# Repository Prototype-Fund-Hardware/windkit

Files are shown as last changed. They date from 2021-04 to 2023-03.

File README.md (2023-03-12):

<div align="center">
  

#### ⚠️ Caution: The windkit is still in development.Prototype not field tested yet!⚠️

#### ⚠️ Project is not recommended for reproduction!⚠️


  

</div>

___

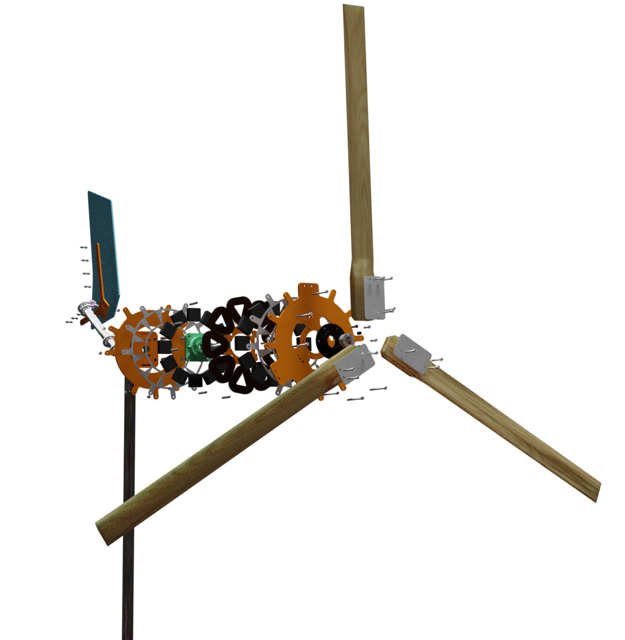
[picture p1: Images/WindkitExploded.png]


## Introduction

The windkit is a small wind turbine to generate electricity from wind energy. It can be used either in offgrid or ongrid applications. Apart from the [aluminium and steel parts](/-/tree/master/Export/LaserCutterFiles) that need to be laser cutted the windkit can be build and maintained using standard hand tools.

### Main features

- **secure**
- **easy to build, repair & maintain**
- **open-source**
- **developed following small wind turbine standard [IEC61400-2:2013](https://webstore.iec.ch/publication/5433)**

### Technical specifications

- **rotor diameter: 2.0 Meter**
- **rated power: 400 Watt @ 11 m/s wind speed**
- **energy production: 200 kWh/a @ 3 m/s annual average wind speed**
- **system voltage: 12, 24, 48 Volt**

For more information check out the [Flyer](./Misc/FlyerWindkit.pdf)!

### What the windkit can and can´t do:

#### What it can´t:

* It will not power your entire house and heat your swimming pool.

* It will not work on a balkony or a roof top.

* It will hardly deliver energy on a site with low or no wind. It's performance would then be like a photo voltaic module placed in a cellar.

#### What it can:

* Supply offgrid places with people who are aware of theire energy consumption. Best in addition with photo voltaic.

* Produce around 800 kWh of electrical energy in windy sights like costal areas or islands.

* Be a fun project of self empowerment.

## Who we are and where we come from

We are the [ERNI-Collective](https://www.erni-kollektiv.org/)  a group of around 10 people based in Germany with various professional backgrounds (renewable-, civil-, environmental-engineer, metalworker, woodworker). We are focusing on educational workshops in the field of renewable energies especially on small wind turbines (SWT). Since 2015, we are conducting educational workshops on how to build, install, operate and maintane SWT based on the plans of [Hugh Piggott](https://scoraigwind.co.uk/a-wind-turbine-recipe-book/). In 1978 Hugh Piggott started to develop a SWT to power his offgrid home in Scotland on Scoraig-Island. Since then he designed various SWT ranging from 1.8 m to 4.2 m rotor diameter and published various Recipe Books and Construction Manuals.

## Development of the windkit

In our educational workshops we mainly build the [2F SWT](https://scoraigwind.co.uk/2014/06/ebook-plans-for-2f-turbine-now-finally-published/) from Hugh Piggott. Its a turbine with 2 m rotor diameter and a generator build with ferrite magnets. Throughout the years we realised that it was difficult for people to follow the DIY-focused building instructions.The idea of a more modular SWT design using standard parts and modern manufacturing technologies (laser cutting) was born.
The result is the windkit. You can find all files of the windkit in this repo as well as a step by step assmebly guide in the [wiki](https://git.erni-kollektiv.org/erni/windkit/-/wikis/1.Introduction).
The generator design of the windkit is still based on the [2F Construction Manual](https://scoraigwind.co.uk/2014/06/ebook-plans-for-2f-turbine-now-finally-published/). The blade design is based on the master thesis of [Performance analysis and improvement of a small locally produced wind turbine for developing countries](file:///C:/Users/imman/Downloads/Nienke%20Hosman%20r.pdf) by N. Hosman.

## Software requirements

#### FreeCAD - view and edit CAD files

windkit is build with realthunder's FreeCAD fork : FreeCAD_assembly3 [2020.08.18](https://github.com/realthunder/FreeCAD_assembly3/releases/tag/0.11). To modify the model we recommend the same or even newer versions. For the assembly process we've been using the assembly workbench Assembly3. The workbench is bundled in the fork mentioned before, no addition installation are needed. In addition we use the Fasteners WB [V0.3.32 03 Sep 2020](https://github.com/shaise/FreeCAD_FastenersWB/tree/bbdcf82e55467523f5533179a896225213b0b5f1) for fasteners groups, this workbench needs to be installed separatly via the Addon-Manager in Freecad. 

#### QCAD - view dxf files

Export files of 2D shapes of the CAD modell for laser cutting have the format ".dxf". This is a common format. To view the .dxf-files download the the open source 2D CAD software [QCAD](https://qcad.org/en/).

#### MarkText - view and edit mark down files

All text files in the windkit repository as well as the windkit wiki are written in [Markdown](https://en.wikipedia.org/wiki/Markdown). To open and edit markdown files, like this README.md, download the mark down editor [MarkText](https://github.com/marktext/marktext).

## Assembly overview

The master assembly file is called `MainAssembly.windkit.FCStd`. All sub-assemblies are saved in different folders. The sub-assemblies are shown in the following image below. The [BOM](./Bom.ods) is also structured the way the Cad is organised.
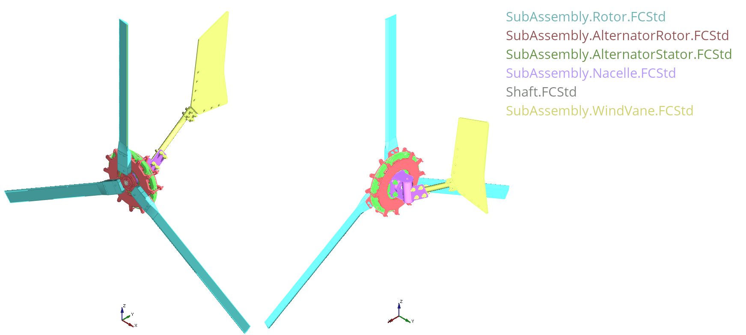
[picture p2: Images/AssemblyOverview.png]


## Prototype

Beginning of 2021 a prototype has been built in a workshop.
The following picture shows all parts of the windkit prototype before assembly. 

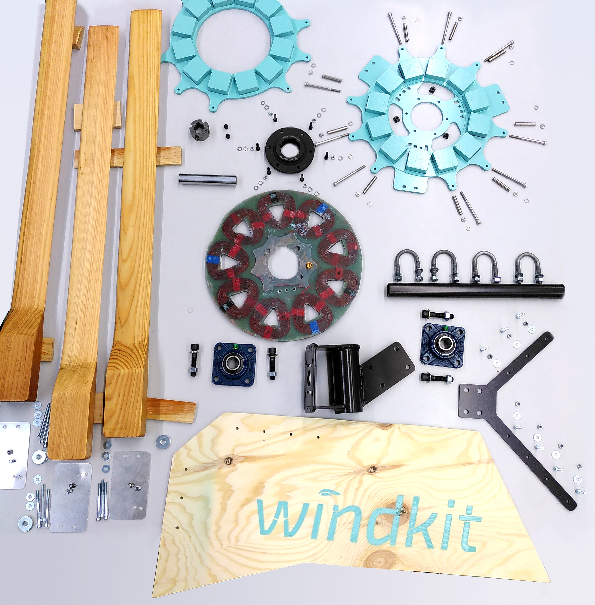
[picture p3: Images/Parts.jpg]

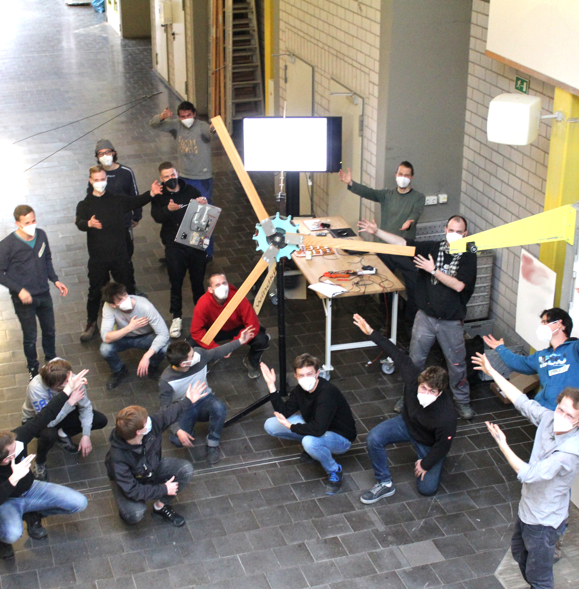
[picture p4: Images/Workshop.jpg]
  

The next step is to bring the turbine to the field for testing!

## Contributing

You want to contribute to our project? That´s great. Check out our [Contributing](https://git.erni-kollektiv.org/erni/windkit/-/wikis/Contributing)  page in our wiki.

## Get in touch with us

You wanna know more about this project or drink a beer with us? Just write us a message info@erni-kollektiv.org

windkit is developed by [ERNI collective](https://www.erni-kollektiv.org/)

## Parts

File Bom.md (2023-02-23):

The bill of materials (BOM) follows the BOM proposal of [DIN SPEC 3105](https://gitlab.com/OSEGermany/oh-tsdc/-/blob/master/OH-TsDC.md) using **TsDC-ID** (technology specific documentation criteria identifier) and unique position numbers to identify each component.

| TsDC-ID Abbreviation | Explanation |
| --- | --- |
| COM | Component |
| ASM | Assembly |
| BUY | Proprietary components |
| STD | Standard components |
| MAN | Self-designed components to manufacture |
| MEC | Mechanic |

| Pos. | Name | Units | TsDC-ID (1) | Reference |
| ---- | --- | ----- | --- | --- |
| 1 | rotor | 1 | ASM-MEC | |
| 1.01 | rotor front mounting plate | 3 | COM-MAN | Laser part, aluminium/stainless steel, 2 mm thick, RotorFrontMountingPlate.dxf |
| | | | | |
| 1.02 | rotor blade | 3 | COM-MAN | larch tree, air-dried, blade measurements: 1050 x 80 x 27 mm |
| | | | | |
| 1.03 | rotor blade fastener bolt | 9 | COM-STD | DIN 912 M6 x 50 mm, property class 8.8, metric bolt, cylinder head with hexagon socket |
| 1.04 | rotor blade fastener slot nut  | 3 | COM-STD | DIN 508-8-M6-8/10, T-Slot-Nut |
| 1.05 | rotor blade fastener nut | 6 | COM-STD | DIN 985 M6, hexagon lock nut, with polyamide clamping piece |
| 1.06 | rotor blade fastener washer | 6 | COM-STD | DIN 125 A M6, 6.4 x 12 x 1.6 mm, washer |
| 1.07 | boiled linseed oil | 1 | COM-BUY | 50 ml |
| 2 | alternator rotor | 1 | ASM-MEC | |
| 2.01 | upwind magnet disc | 1 | COM-MAN | Laser part, steel S235 or S355, 6 mm thick, no surface treatment, UpwindMagnetDiscSlotNut.dxf |
| 2.02 | taper bush | 1 | COM-BUY | Article ID.: 62250325,Taper bush 1210, bore 25 mm |
| 2.03 | taper bush setscrew | 2 | COM-STD | part of the scope of delivery of the taper bush, see pos. 2.02 |
| 2.04 | taper bush hub | 1 | COM-BUY | Article ID.: 14090120, Taper bush hub for Taper Bush size 1210, 120 mm outer diameter |
| 2.05 | taper bush hub fastener bolt | 6 | COM-STD | DIN 912 M6 x 25 mm, property class 8.8, cylinder head with hexagon socket |
| 2.06 | taper bush hub fastener nut | 6 | COM-STD | DIN 985 M6, hexagon lock nut, with polyamide clamping piece |
| 2.07 | taper bush hub fastener washer | 12 | COM-STD | DIN 125 A, for M6, 6.4 x 12 x 1.6 mm, washer |
| 2.08 | magnet stencil | 2 | COM-MAN | Laser part, aluminium/stainless steel, 2 mm thick, MagnetStencil.dxf |
| 2.09 | ferrite magnet | 24 | COM-BUY | Ferrit Magnet 50 x 50 x 20 mm |
| 2.10 | spacer sleeve | 9 | COM-BUY | Stainless steel sleeves 8 x 6 x 1 mm (up to M6), 50 mm length |
| 2.11 | discs fastener bolt | 9 | COM-STD | DIN 912 M6 x 85 mm, stainless Steel A2, metric bolt, cylinder head with hexagon socket |
| 2.12 | discs fastener nut | 9 | COM-STD | DIN 985 M6, stainless Steel A2, hexagon lock nut, with polyamide clamping piece |
| 2.13 | discs fastener washer | 18 | COM-STD | DIN 125 A, for M6, 6.4 x 12 x 1,6 mm, stainless steel A2, washer |
| 2.14 | downwind magnet disc | 1 | COM-MAN | Laser part, steel S235 or S355, 6 mm thick, no surface treatment, DownwindMagnetDisc.dxf |
| 2.15 | two component epoxy adhesive | 2 | COM-BUY | Two-component epoxy adhesive, min. 45 min hardening time |
| 2.16 | exterior metal paint | 1 | COM-BUY | 200 ml |
| 3 | shaft | 1 | COM-BUY | "Precision shaft steel CF53, hardened,  dressed to size, chromed, 25 (h7) x 1000mm: 64762500, per windkit 125 mm needed |
| 4 | alternator stator | | | |
| 4.01 | mounting inlay | 1 | COM-MAN | Laser part, steel S235 or S355, 6 mm thick, no surface treatment, MountingInlayUkf205Mt60.dxf |
| 4.02 | stator cast | 1 | COM-BUY | Epoxy resin and hardener, approx. 1.4 l |
| 4.03 | copper wire coils | 9 | COM-BUY | Approx. 3.6 kg of copper wire, 1.6 mm Diameter, Grade 2, 200°C heat resistant, approx. 400 g per coil, approx. 3.6 kg per windkit needed |
| 4.04 | mounting inlay fastener bolt | 4 | COM-STD | DIN 912 M12 x 60 mm, property class 8.8, metric bolt, cylinder head with hexagon socket |
| 4.05 | Mounting inlay fastener nut | 4 | COM-STD | DIN 985 M12, hexagon lock nut, with polyamide clamping piece |
| 4.06 | mounting inlay fastener washer | 8 | COM-STD | DIN 125 A, for M12, 13 x 24 x 2,5 mm, washer |
| 4.07 | stator plug | 1 | COM-BUY | MT60 connector, male part |
| 4.08 | exterior paint | 1 | COM-BUY | 100 ml |
| 5 | nacelle | 1 | ASM-MEC | |
| 5.01 | housing bearing | 2 | COM-BUY | UKF205, ball bearing unit with cast metal housing, locking on shaft via set screw |
| 5.02 | bearing mounting plate | 1 | COM-MAN | Laser part, steel S235 or S355, 6 mm thick, no surface treatment, BearingMountingPlateUkf205.dxf |
| 5.03 | upper spacer | 1 | COM-MAN | Laser part, steel S235 or S355, 6 mm thick, no surface treatment, UpperSpacer.dxf |
| 5.04 | lower spacer | 1 | COM-MAN | Laser part, steel S235 or S355, 6 mm thick, no surface treatment, LowerSpacer.dxf |
| 5.05 | yaw pipe | 1 | COM-BUY | Cylindric pipe, steel, no surface treatment, 60.3 x 3.65 x 140 mm |
| 5.06 | cable gland | 1 | COM-BUY | M25 x 1.5, cable range 9.0 - 16.0 mm |
| 5.07 | wind vane socket | 1 | COM-MAN | Laser part, steel S235 or S355, 6 mm thick, no surface treatment, WindVaneSocket.dxf |
| 5.08 | exterior metal paint | 1 | COM-BUY | |
| 6 | wind vane | 1 | ASM-MEC | |
| 6.01 | vane | 1 | COM-MAN | plywood, birch waterproof glued BFU100, 650 x 350 x 6 mm |
| 6.02 | vane pipe | 1 | COM-BUY | Cylindric pipe, steel, no surface treatment, 33.7 x 2.5 x 400 mm |
| 6.03 | vane mounting | 1 | COM-MAN | Laser part, steel S235 or S355, 6 mm thick, no surface treatment, VaneMounting.dxf |
| 6.04 | vane fastener bolt | 7 | COM-STD | DIN 912 M6 x 25 mm, property class 8.8, metric bolt, cylinder head with hexagon socket |
| 6.05 | vane fastener nut | 7 | COM-STD | DIN 985 M6, hexagon lock nut, with polyamide clamping piece |
| 6.06 | vane fastener washer | 14 | COM-STD | DIN 125 A, for M6, 6.4 x 12 x 1.6 mm, washer |
| 6.07 | u bolt clamp bolt | 4 | COM-STD | DIN 3570, Form A, nominal size DN25, dimension A = 38 mm, M10, steel strap for tubes, for pipe outer diameter 30 -34 mm |
| 6.08 | u bolt clamp washer | 8 | COM-STD | DIN985 M10, hexagon lock nut, with polyamide clamping piece |
| 6.09 | u bolt clamp nut | 8 | COM-STD | DIN 125 A, for M10, washer |
| 6.10 | boiled linseed oil | 1 | COM-BUY | 50 ml |
| 6.11 | exterior wood paint | 1 | COM-BUY | 200 ml |

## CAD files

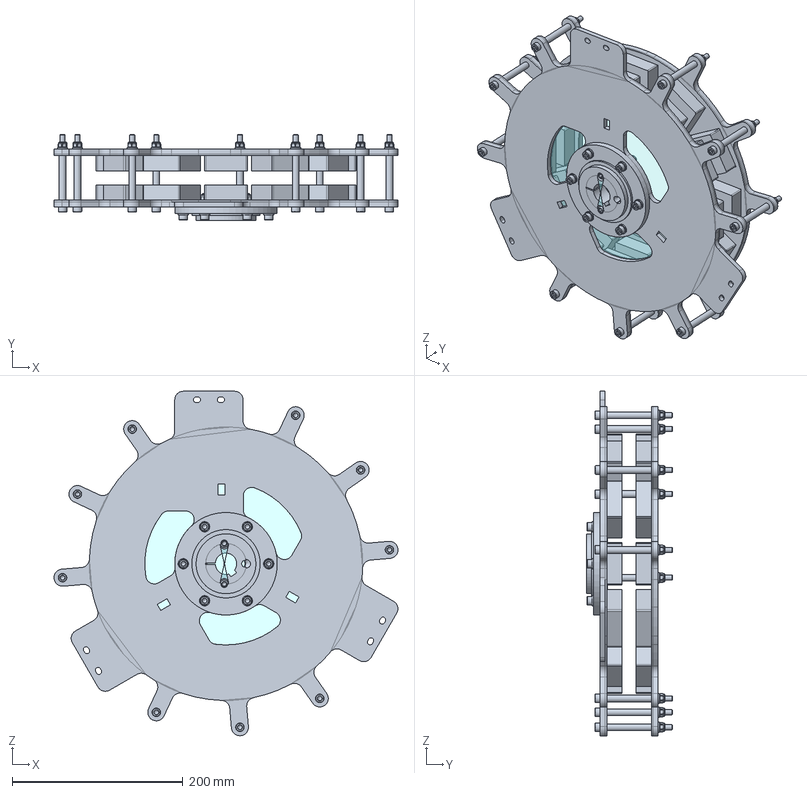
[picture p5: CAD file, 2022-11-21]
Cad/AlternatorRotor/SubAssembly.AlternatorRotor.FCStd
402.6 x 101.0 x 403.2 mm
Parts
CircleFront@MagnetArray_
_SetscrewHoleFront@TaperBush_
CircleFront@MagnetArray_001

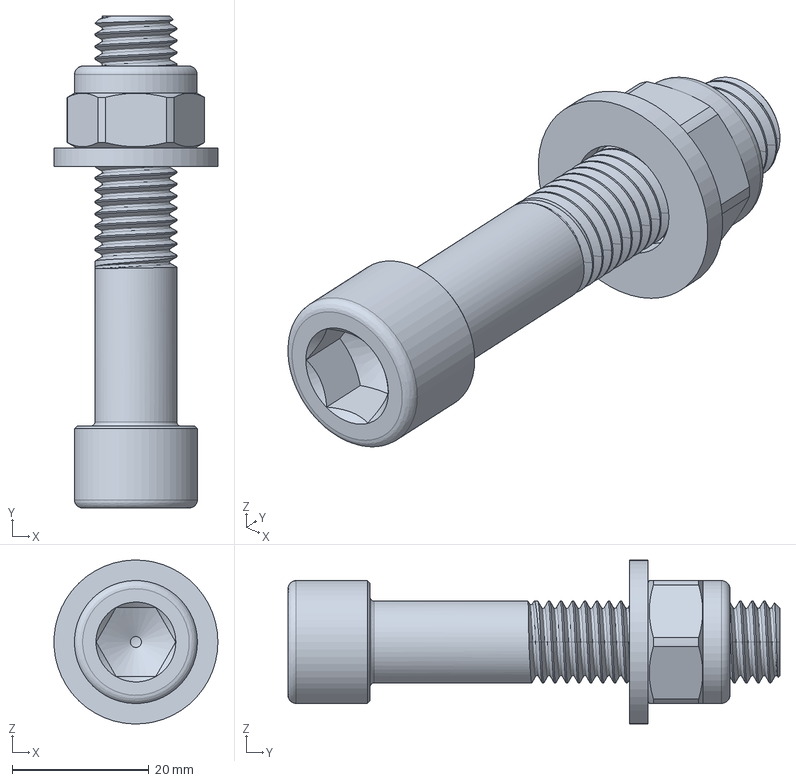
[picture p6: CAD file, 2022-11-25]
Cad/AlternatorStator/FastenerAssembly.MountingInlay.FCStd
24.0 x 72.0 x 24.0 mm

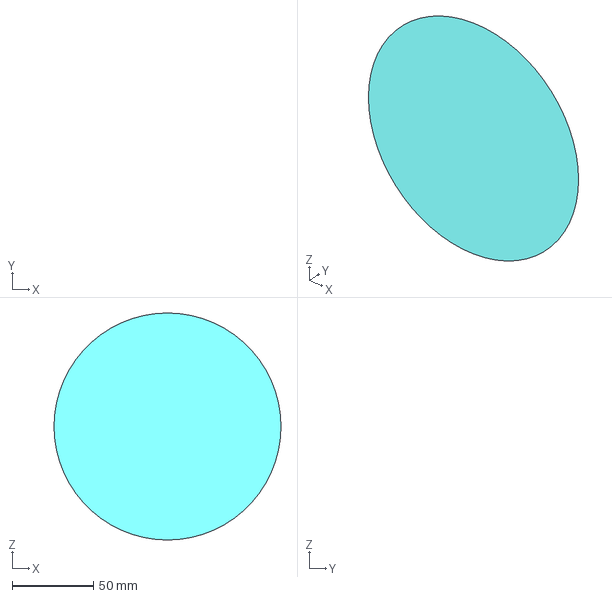
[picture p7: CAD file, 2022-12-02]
Cad/MainAssembly.windkit.FCStd
140.0 x 0 x 140.0 mm

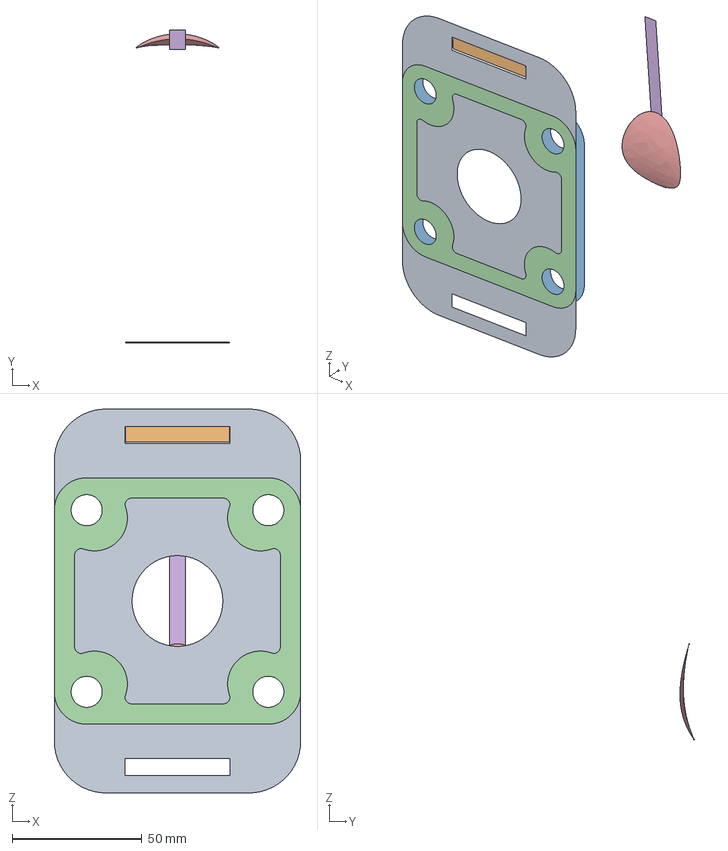
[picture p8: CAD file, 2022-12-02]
Cad/Nacelle/SubAssembly.Nacelle.FCStd
95.0 x 120.6 x 148.0 mm
FrontSurface@BearingMountingPlate_
SurfaceFront@UpperSpacer_
_Element020
_Element021
CircleFont@WindVaneSocket_
SurfaceFront@WindVaneSocket_rev2_

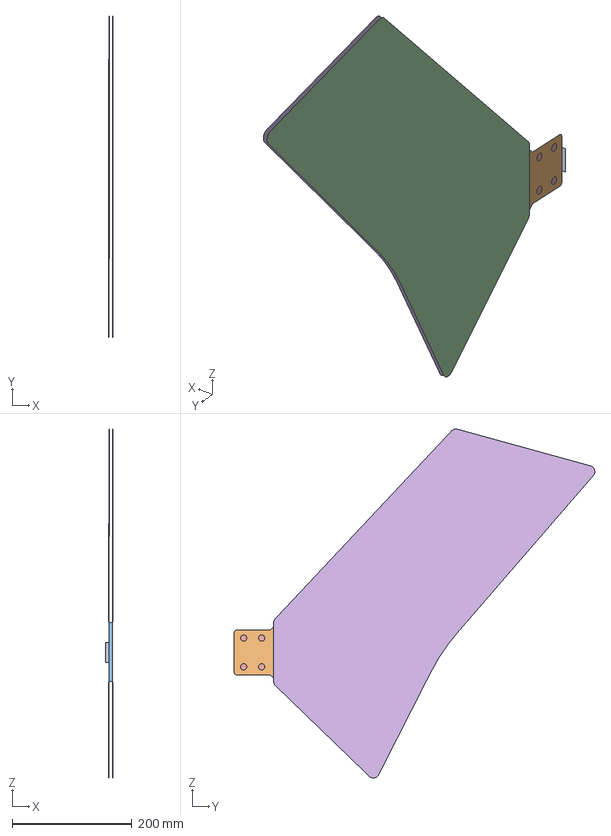
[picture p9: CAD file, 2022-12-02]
Cad/WindVane/SubAssembly.WindVane.FCStd
12.0 x 601.8 x 582.2 mm
SurfaceFront@VaneMounting_
_Element016
LowerSurfaceFront@Vane_
SurfaceLeft@Vane_
SurfaceRight@VaneMounting_
_Element027

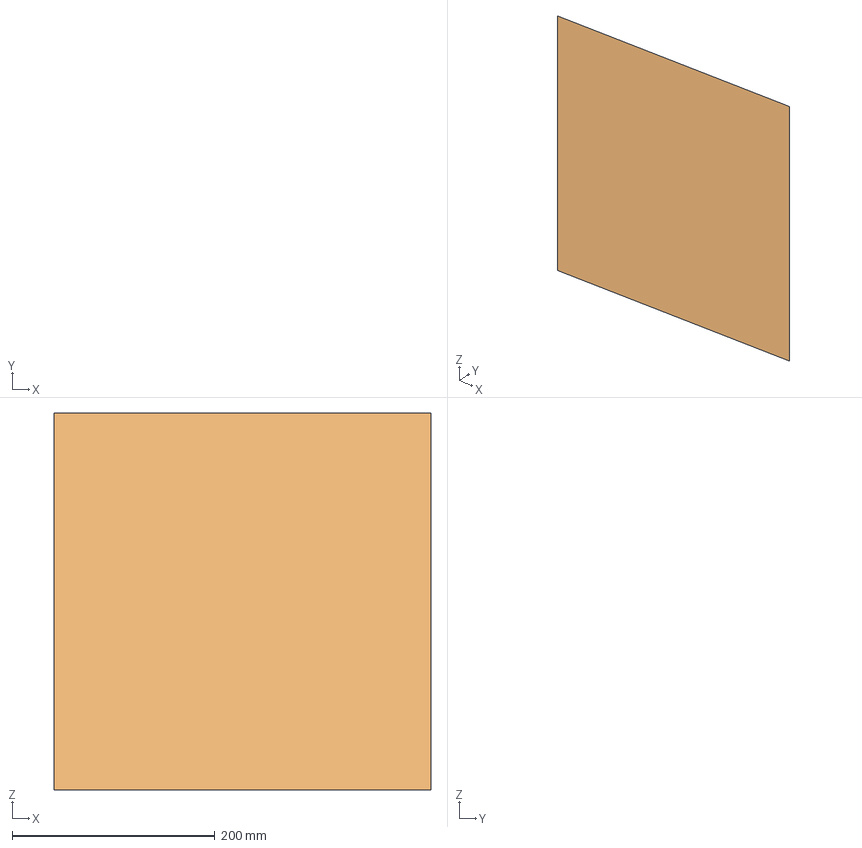
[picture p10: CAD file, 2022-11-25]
Cad/AlternatorStator/SubAssembly.AlternatorStator.FCStd
372.0 x 8.2e-14 x 372.0 mm
XZ_Plane@CoilsArray_
XZ_Plane@StatorCast_

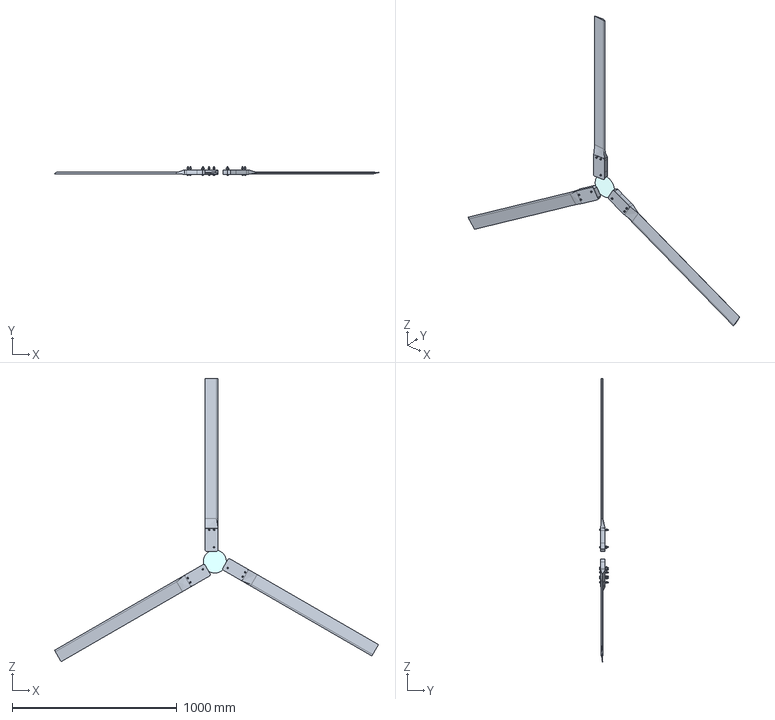
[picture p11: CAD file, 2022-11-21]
Cad/Rotor/SubAssembly.Rotor.FCStd
1966.0 x 56.0 x 1720.0 mm
Parts
CircleRear@RotorArray_

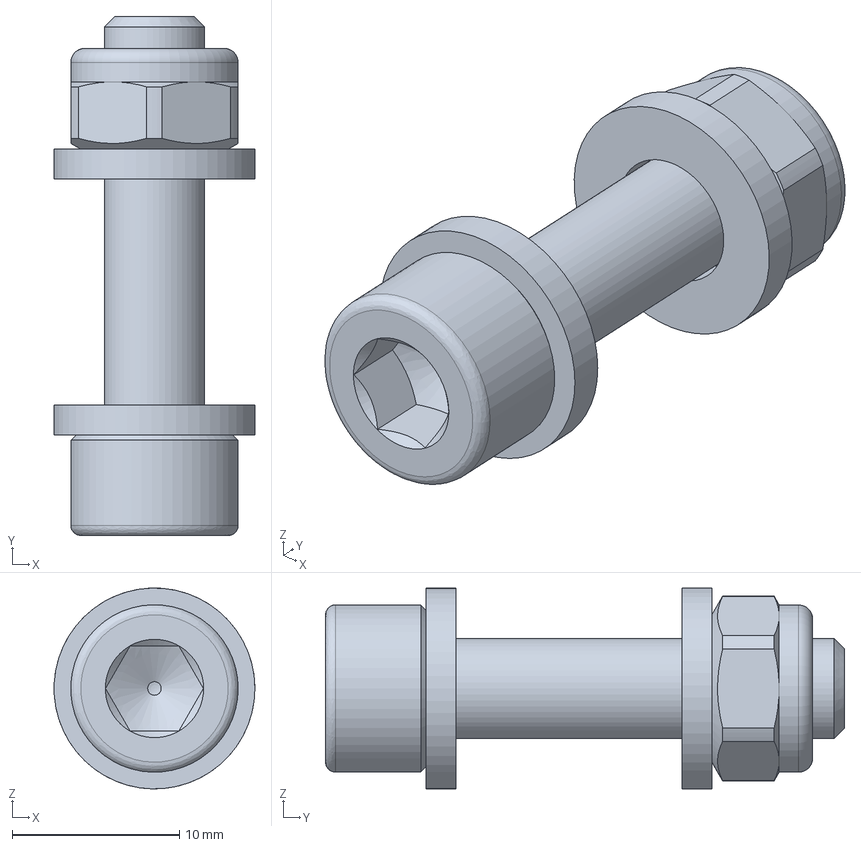
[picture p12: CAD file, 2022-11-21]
Cad/AlternatorRotor/FastenerAssembly.TaperBushHub.FCStd
12.0 x 31.0 x 12.0 mm

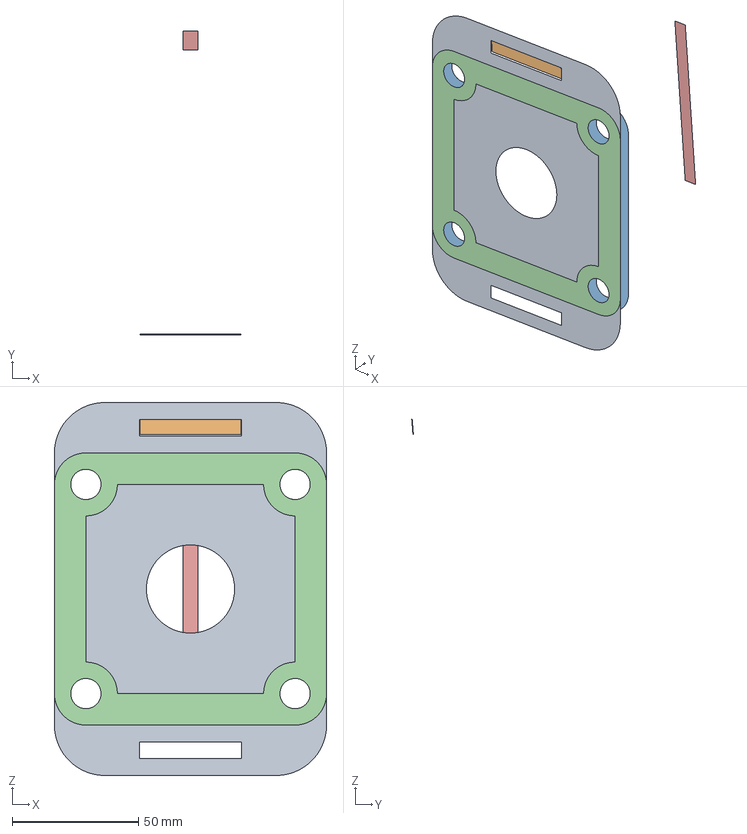
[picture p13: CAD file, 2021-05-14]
Cad/Nacelle/SubAssembly.Nacelle.TechDraw.FCStd
108.0 x 120.6 x 148.0 mm
FrontSurface@BearingMountingPlate_
SurfaceFront@UpperSpacer_
_Element020
_Element021
SurfaceFront@WindVaneSocket_rev2_

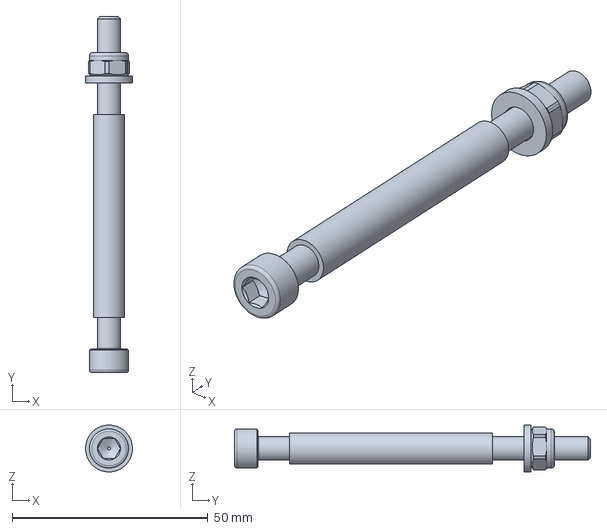
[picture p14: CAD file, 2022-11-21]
Cad/AlternatorRotor/FastenerAssembly.Disc.FCStd
12.0 x 91.0 x 12.0 mm

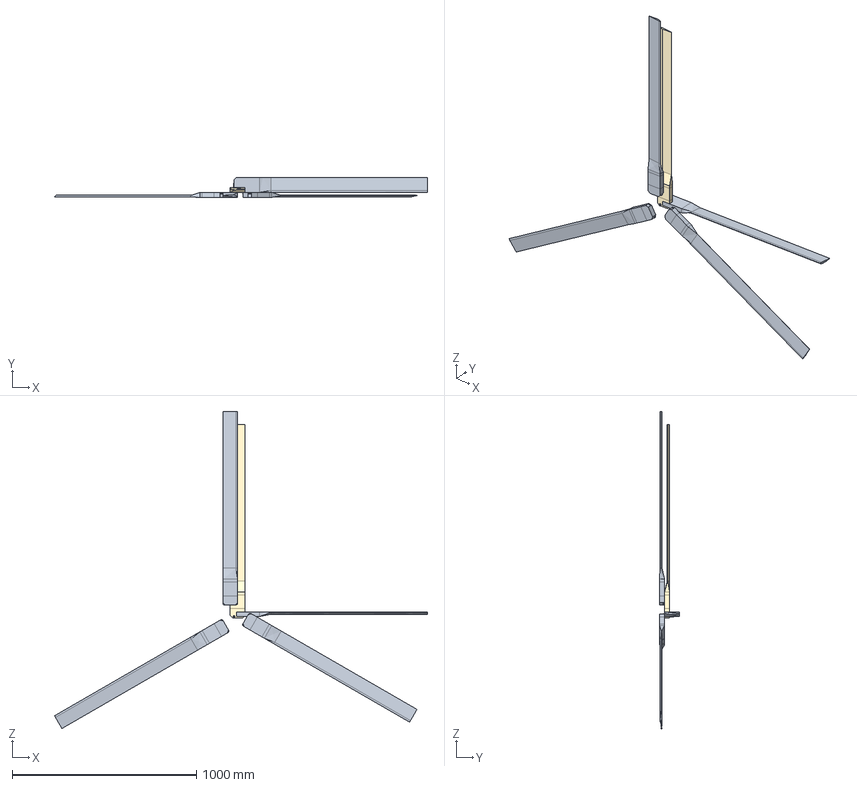
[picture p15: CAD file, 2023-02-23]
Cad/Rotor/Components.Rotor.FCStd
2023.0 x 107.0 x 1720.0 mm
Parts
Parts001
Parts003
Parts005
Parts008

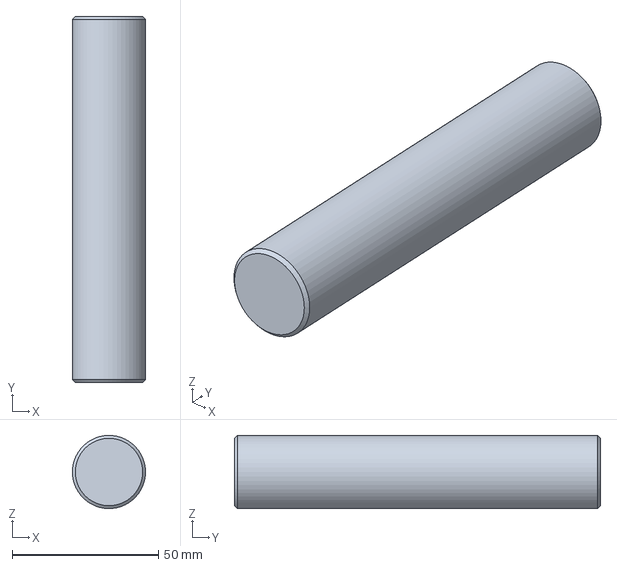
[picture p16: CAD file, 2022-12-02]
Cad/Shaft/Shaft.FCStd
25.0 x 125.0 x 25.0 mm
Parts

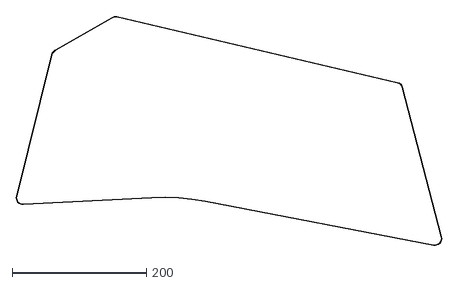
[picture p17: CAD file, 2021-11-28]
Export/LaserCutterFiles/VanePlywood6mm1Pcs.dxf
634.7 x 341.5

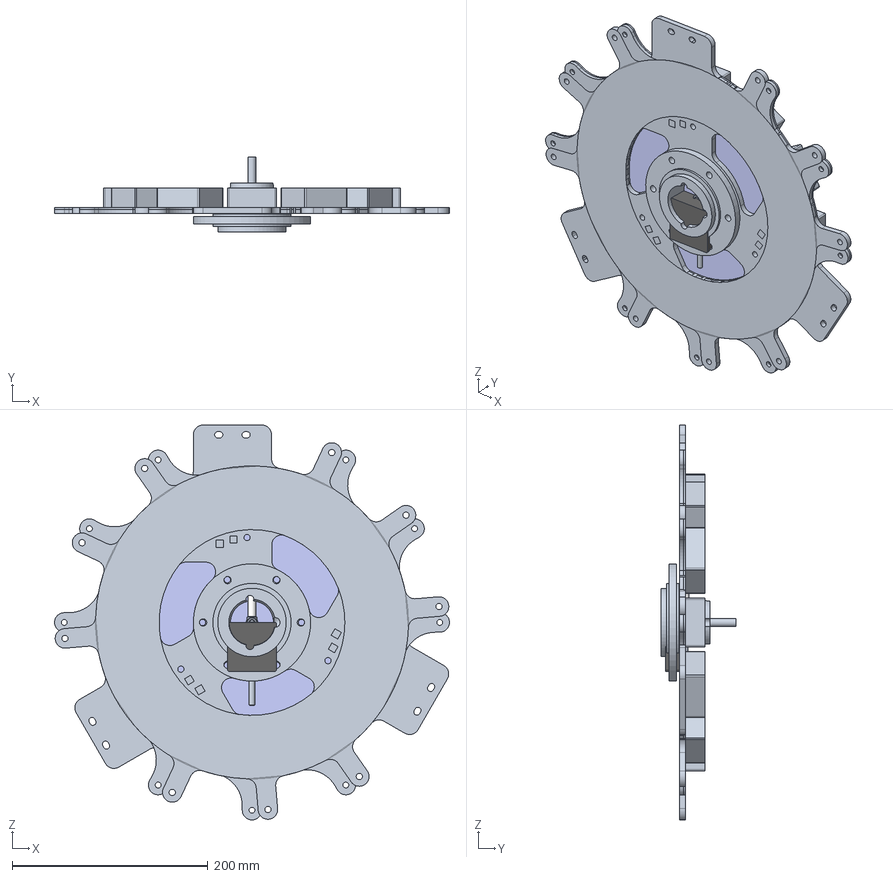
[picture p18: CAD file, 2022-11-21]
Cad/AlternatorRotor/Components.AlternatorRotor.FCStd
404.0 x 77.0 x 403.9 mm
FerritMagnet
Circle002
CircleFront
Parts
Parts001
Parts002
Parts003
Parts004
Parts005
Parts006
Parts007
Parts008
Parts009
Parts010
Parts011
Parts012
Parts013
Parts014
Parts015
Parts016

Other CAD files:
Cad/WindVane/FastenersAssembly.Vane.FCStd
Cad/Nacelle/Components.Nacelle.FCStd
Cad/WindVane/Components.WindVane.FCStd
Export/LaserCutterFiles/RotorFrontMountingPlateAluminium2mm3Pcs.dxf
Cad/AlternatorRotor/Components.AlternatorRotor.TechDraw.FCStd
Cad/AlternatorStator/Components.AlternatorStator.FCStd
Cad/AlternatorStator/Components.AlternatorStator.TechDraw.FCStd
Cad/Nacelle/Components.Nacelle.TechDraw.FCStd
Cad/Rotor/Components.Rotor.TechDraw.FCStd
Cad/Rotor/Fastener.RotorBlade.FCStd
Cad/Rotor/Fastener.RotorBladeSlotNut.FCStd
Cad/Rotor/Rotor.FCStd
Cad/Rotor/RotorArray.FCStd
Cad/Rotor/RotorBladeBolt.FCStd
Cad/Rotor/RotorBladeNut.FCStd
Cad/Rotor/RotorBladeWasher.FCStd
Cad/Rotor/RotorFrontMountingPlate.FCStd
Cad/WindVane/FastenersAssembly.UBoltClamp.FCStd
Export/LaserCutterFiles/BearingMountingPlateS235Steel6mm2Pcs.dxf
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

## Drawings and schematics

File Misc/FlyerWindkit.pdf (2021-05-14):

## the hackable wind turbine

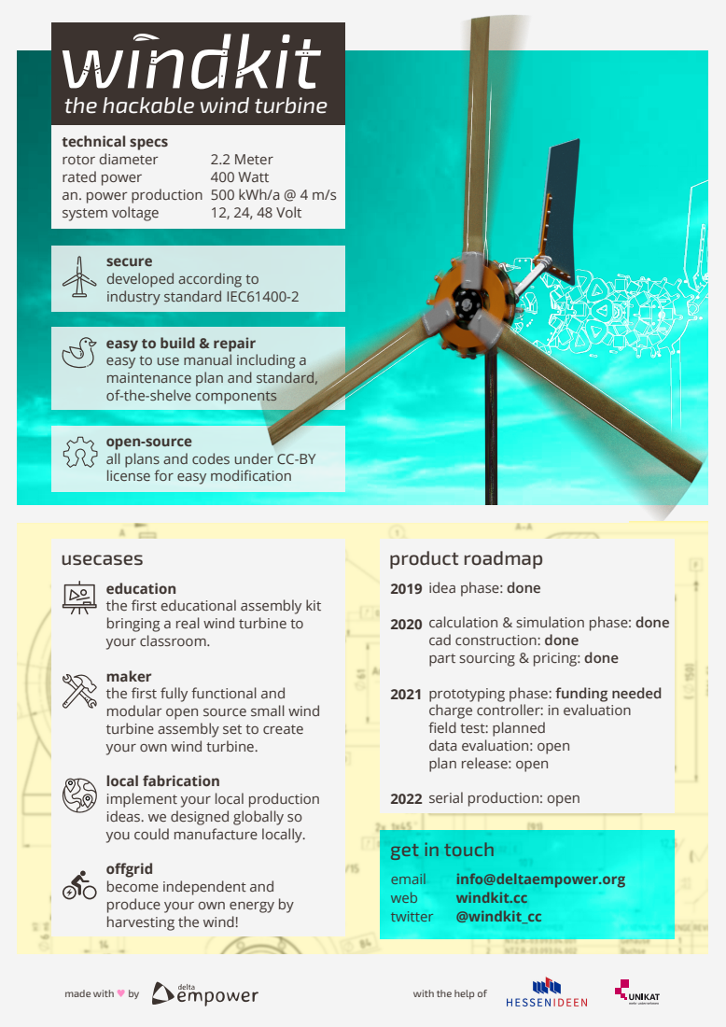
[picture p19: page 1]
usecases; product roadmap; made with ♥ by; with the help of; 2.2 Meter 400 Watt 500 kWh/a @ 4 m/s 12, 24, 48 Volt

technical specs
rotor diameter
rated power
an. power production
system voltage

secure
developed according to
industry standard IEC61400-2

easy to build & repair
easy to use manual including a
maintenance plan and standard,
of-the-shelve components

open-source
all plans and codes under CC-BY
license for easy modification

education
the first educational assembly kit
bringing a real wind turbine to
your classroom.
maker
the first fully functional and
modular open source small wind
turbine assembly set to create
your own wind turbine.
local fabrication
implement your local production
ideas. we designed globally so
you could manufacture locally.
offgrid
become independent and
produce your own energy by
harvesting the wind!

idea phase: done
calculation & simulation phase: done
cad construction: done
part sourcing & pricing: done
charge controller: in evaluation
field test: planned
data evaluation: open
plan release: open

prototyping phase: funding needed

serial production: open

get in touch
email
web
twitter

info@deltaempower.org
windkit.cc
@windkit_cc

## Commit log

2021-04-28 added AssemblyOverview
2021-05-04 Dateien hochladen nach „“
    [windkit_bom.ods]
2021-05-04 „README.md“ ändern
2021-05-04 „LICENCE“ hinzufügen
2021-05-14 Added Cad files
    [Bom.ods, Components.AlternatorRotor.FCStd, Components.AlternatorRotor.TechDraw.FCStd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]
2021-11-28 Upload New File
    [_BearingMountingPlateUkf205_1Stk.dxf]
2021-11-28 Replace Bom.ods
    [Bom.ods]
2022-11-18 coloring the wind vane
    [Components.WindVane.FCStd, FastenersAssembly.UBoltClamp.FCStd, FastenersAssembly.Vane.FCStd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]
2022-11-18 coloring shaft (not working well jet)
    [Shaft.FCStd]
2022-11-18 coloring rotor
    [Components.Rotor.FCStd, Fastener.RotorBlade.FCStd, SubAssembly.Rotor.FCStd]
2022-11-18 coloring nacelle
    [Components.Nacelle.FCStd, SubAssembly.Nacelle.FCStd]
2022-11-18 coloring alternatorstator
    [Components.AlternatorStator.FCStd, FastenerAssembly.ElectricConnection.FCStd, FastenerAssembly.MountingInlay.FCStd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]
2022-11-21 fix coil sketch
    [Components.AlternatorStator.FCStd]
2022-11-21 colored AlternatorStator + added fillet to statorCast
    [Components.AlternatorStator.FCStd, SubAssembly.AlternatorStator.FCStd]
2022-11-21 exchanged MountingInlay to UKF205
    [Components.AlternatorStator.FCStd, FastenerAssembly.ElectricConnection.FCStd, SubAssembly.AlternatorStator.FCStd]
2022-11-21 added MT60 (statorplug)
    [Components.AlternatorStator.FCStd, FastenerAssembly.ElectricConnection.FCStd, SubAssembly.AlternatorStator.FCStd]
2022-11-21 coloring alternator rotor
    [Components.AlternatorRotor.FCStd, FastenerAssembly.Disc.FCStd, FastenerAssembly.TaperBushHub.FCStd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]
2022-11-21 coloring rotor and windvane in woodish color
    [Components.Rotor.FCStd, Components.WindVane.FCStd]
2022-11-21 update mainassembly
    [Components.AlternatorRotor.FCStd, MainAssembly.windkit.FCStd, SubAssembly.AlternatorRotor.FCStd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]
2022-11-21 added UCF205 and exchanged it with UKF205
    [Components.Nacelle.FCStd, SubAssembly.Nacelle.FCStd]
2022-11-21 rotated AlternatorStator
    [MainAssembly.windkit.FCStd, SubAssembly.AlternatorRotor.FCStd, SubAssembly.Nacelle.FCStd]
2022-11-21 added slotnut, added UpwindMagnetDiskSlotNut, added Fastener.RotorBladeSlotNut, exchanged and assembled
    [Components.AlternatorRotor.FCStd, Components.Rotor.FCStd, Fastener.RotorBlade.FCStd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]
2022-11-21 assembled UpwindMagnetDiskSlotNut
    [MainAssembly.windkit.FCStd, SubAssembly.AlternatorRotor.FCStd, SubAssembly.Nacelle.FCStd]
2022-11-21 added paint groups
    [MainAssembly.windkit.FCStd, SubAssembly.AlternatorRotor.FCStd, SubAssembly.Nacelle.FCStd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]
2022-11-21 revert paining
    [Components.Nacelle.FCStd, SubAssembly.AlternatorRotor.FCStd, SubAssembly.Nacelle.FCStd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]
2022-11-21 Added Wires
    [Components.AlternatorStator.FCStd, SubAssembly.AlternatorStator.FCStd]
2022-11-25 Removed ElectricConnectionInlay and adapted MountingInlay
    [Components.AlternatorStator.FCStd, SubAssembly.AlternatorStator.FCStd]
2022-11-25 updated wires
    [SubAssembly.AlternatorStator.FCStd]
2022-11-25 Removed FastenerAssembly.ElectricConnection.FCStd
    [FastenerAssembly.ElectricConnection.FCStd, SubAssembly.AlternatorStator.FCStd]
2022-11-25 fix stator
    [FastenerAssembly.MountingInlay.FCStd, SubAssembly.AlternatorStator.FCStd]
2022-12-02 replaced ufc 205 cad file
    [Components.Nacelle.FCStd]
2022-12-02 added m25 cable gland
    [Components.Nacelle.FCStd, SubAssembly.Nacelle.FCStd]
2022-12-02 changed display view to solid in shaft
    [Components.Nacelle.FCStd, MainAssembly.windkit.FCStd, Shaft.FCStd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]
2022-12-09 Replace Bom.ods with BOM.md: BOM according to DIN-SPEC3105. Colums reduced to Pos, Name, Units, TsDC-ID, Reference. Component list in line with CAD modell.
    [Bom.ods]
2022-12-09 Change file name from Bom.ods to Bom.md
2023-02-16 Change file names of all dxf files
    File name change according to pattern NameMaterialThicknessAmount e.g. VanePlywood6mm1Pcs.
    [BearingMountingPlateS235Steel6mm2Pcs.dxf, BearingMountingPlateUkf205S235Steel6mm1Pcs.dxf, DownwindMagnetDiscS235Steel6mm1Pcs.dxf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]
2023-02-16 Change file location of dxf files in one main folder LaserCutterFiles.
    [MagnetStencilAluminium2mm2Pcs.dxf, RotorFrontMountingPlateAluminium2mm3Pcs.dxf]
2023-02-16 Resort dxf-files from SteelS235_6mm folder one folder structure upwards.
    [BearingMountingPlateS235Steel6mm2Pcs.dxf, BearingMountingPlateUkf205S235Steel6mm1Pcs.dxf, DownwindMagnetDiscS235Steel6mm1Pcs.dxf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]
2023-02-16 Move file one folder structure upwards.
    [VanePlywood6mm1Pcs.dxf]
2023-02-23 Added substractive RotorBlade model to Components, not used jet in Sub-/MainAssembly!
    [Components.Rotor.FCStd]

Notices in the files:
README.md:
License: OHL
